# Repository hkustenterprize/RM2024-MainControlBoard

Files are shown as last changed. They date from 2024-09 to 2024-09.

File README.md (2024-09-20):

<div align='center'>
    <h1>灵活, 小巧, 可靠</h1>
</div>

<div align='center'>
    <h2>RM2024香港科技大学ENTERPRIZE</h2>
</div>

<div align='center'>
    <h1>G4主控板硬件开源</h1>
</div>

<div align='center'>

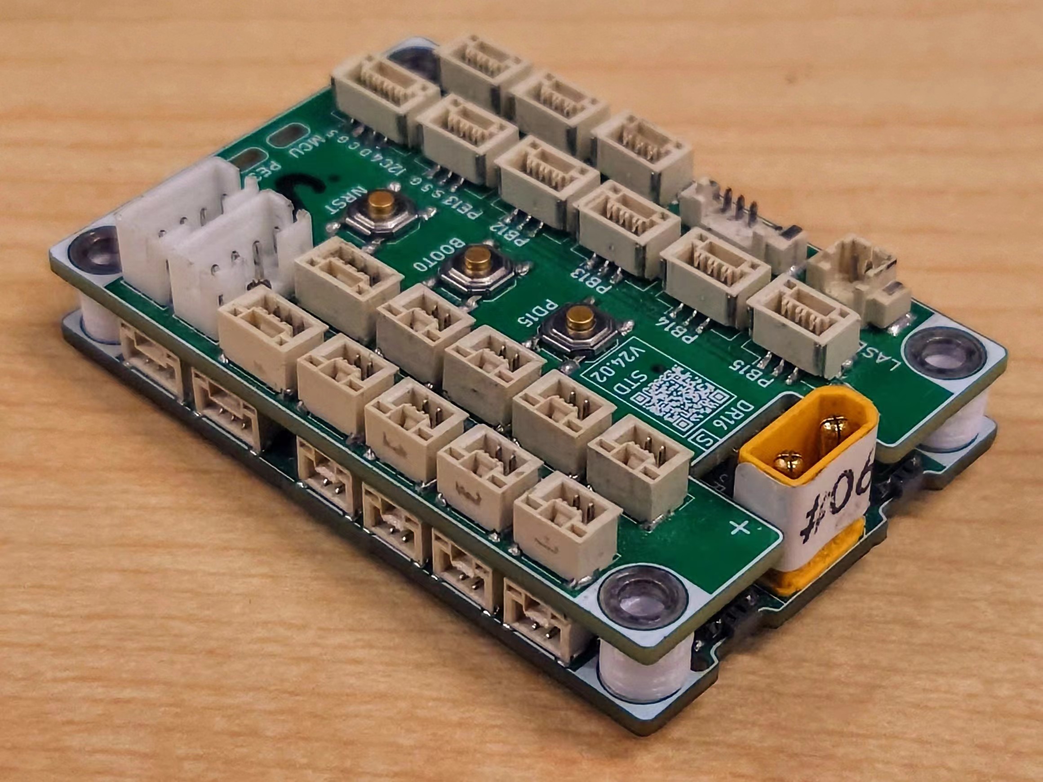
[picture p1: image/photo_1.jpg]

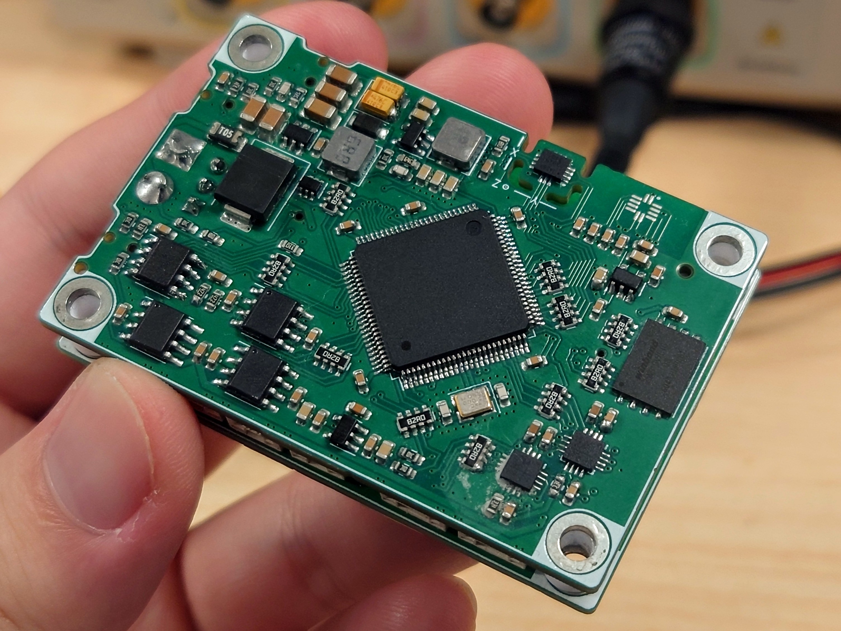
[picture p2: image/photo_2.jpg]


</div>

> 设计者：xzm/贤梓铭 zxianaa@connect.ust.hk
>
> 指导/提议：jyc/EthenJ, jason chan, ry/EEASEE, ofr, gzl/Fallengold, zzy
>
> 香港科技大学ENTERPRIZE战队 robomasterhkust@gmail.com

## 开源内容

~~~
RM2024_MainControlBoard
├── image
├── PDF Schematic               > PDF格式的原理图
├── RM2024_G473_MCB             > 核心板工程文件
├── RM2024_G473_MCB_Debugger    > 调试小板工程文件
├── RM2024_G473_MCB_EngExtend   > 单板方案工程扩展板工程文件 by ofr
├── RM2024_G473_MCB_StdExtend   > 常规扩展板工程文件
├── RM2024_G473_MCB_Shim.step   > 一体3D打印垫片step文件 by tsl
├── RM2024-Template-G473.ioc    > CubeMX模板
├── LICENSE
└── README.md
~~~

开源工程文件设计软件为 KiCAD, 建议使用 **KiCAD 8.0** 打开, 可以导入 **立创EDA**

每个工程文件文件夹中的内容:

~~~
xxx
├── bom             > 焊接小工具, 由 "Interactive HTML BOM" 插件生成
├── production      > 生产文件, 由 "Fabrication Toolkit" 插件生成
├── xxx.kicad_pcb   > PCB
├── xxx.kicad_pro   > 主工程, 通过双击这个启动KiCAD
└── xxx.kicad_sch   > 原理图
~~~

## 方案简介

整套主控板分为核心板(下板)和扩展板(上板), 两板之间使用80pin BTB接口连接; 核心板包含所有核心芯片, 而扩展板一般只用于引出接口 (以及buzzer, laser等功能), 需要特殊功能时则用作功能扩展

- MCU: STM32G473VET6
- IMU: ICM-42688P
- 磁力计: LIS3MDLTR
- TTL (硬件流控): CH343P *2 
- FDCAN *3
- RS485 (硬件流控) *1
- FLASH: W25N01GVZEIG

## 项目背景 & 应用情况

在 RoboMaster 2024 赛季, 由于队内自研的上一代主控板 (F407) 已经无法满足对机器人控制的需求, 于是产生了设计新型主控板的需求

在经过反复考虑和对比后, 我们选择了STM32G473VET6作为主控芯片, 主要原因如下

- 共有三路FDCAN外设, 可以控制更多电机
- 支持RS485硬件流控功能, 提升板间通讯的稳定性
- 相较于H7系列复杂度较低, 开发难度与F4系列近似

同时, 新一代主控板也有缩小体积的需求, 整个主控板大小控制在 **60×40×21mm**, 与大疆C板相近, 便于机械安装

<div align='center'>
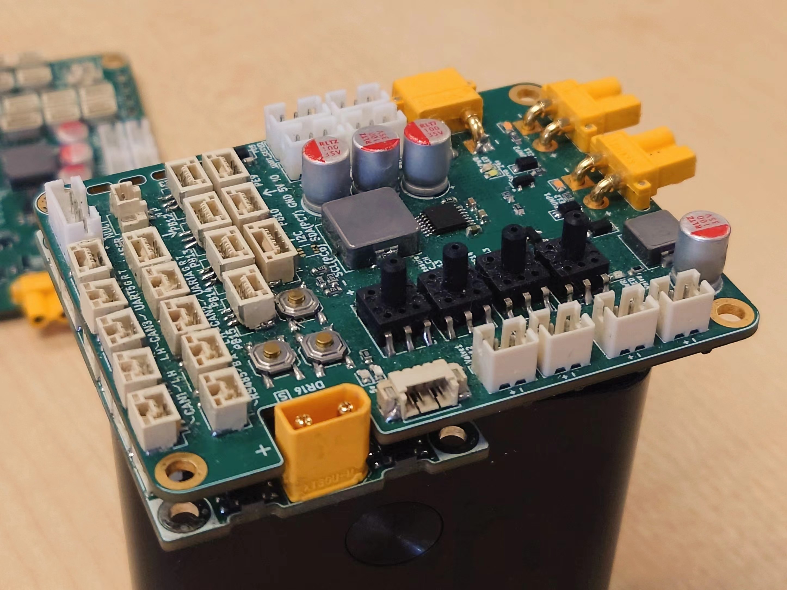
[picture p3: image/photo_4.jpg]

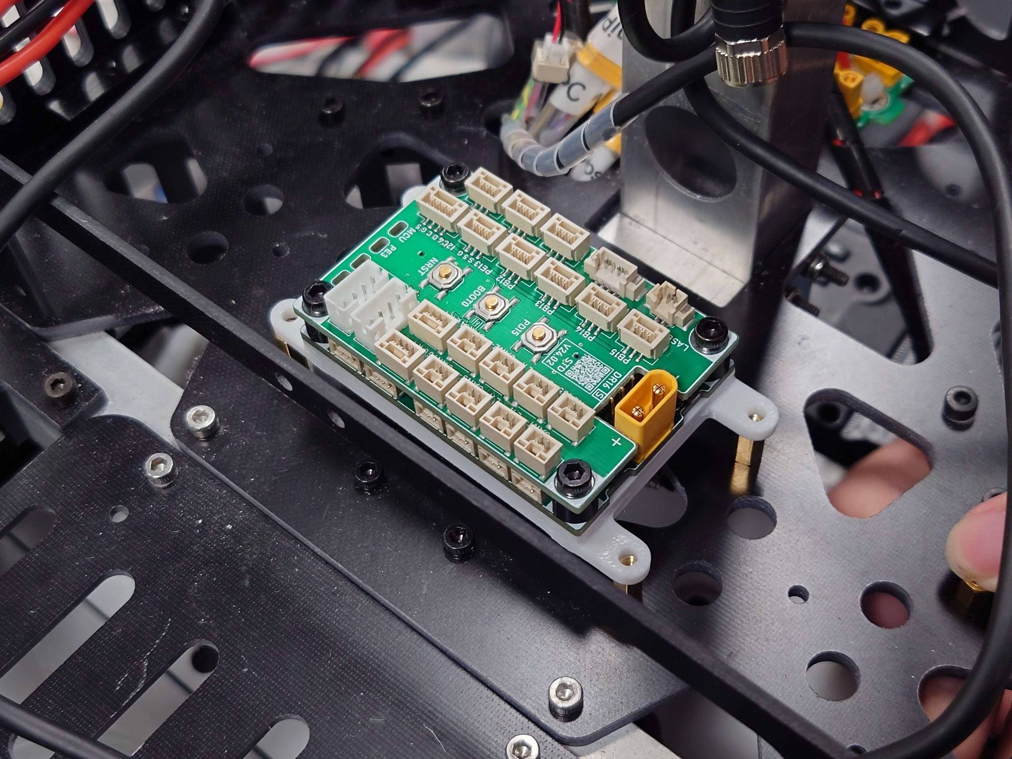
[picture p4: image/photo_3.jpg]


</div>

最终, G4主控板被应用于ENTERPRIZE战队本赛季所有新研发的机器人, 并且为 **工程机器人的单板方案** (左图) 和 **双头哨兵** (右图) 打下基础; 同时也实现了较强的稳定性, 在几场比赛中从未出现因硬件不稳定而导致的问题

## 硬件连接框图(简化)

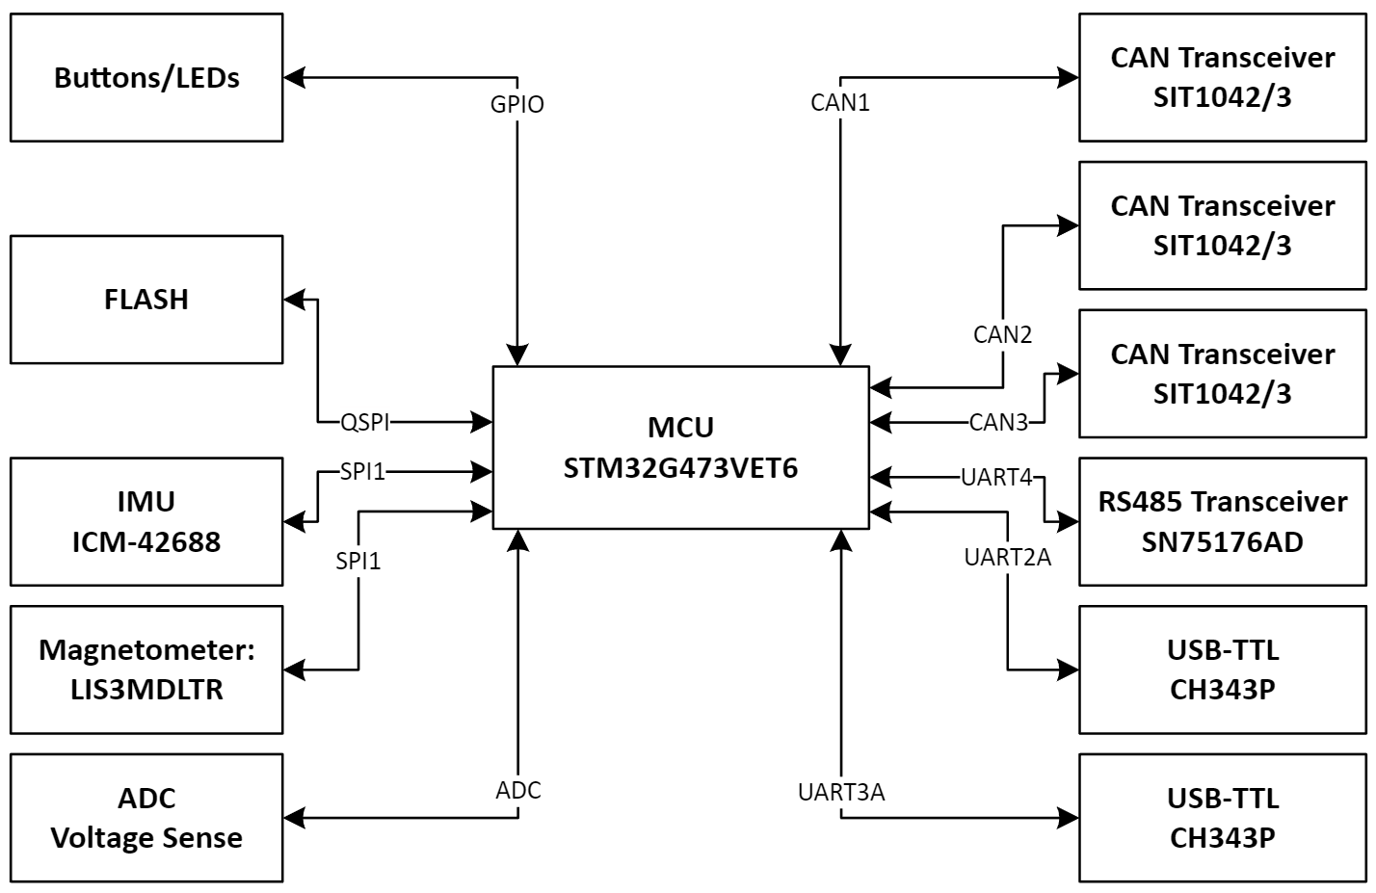
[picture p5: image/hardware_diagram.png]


## 技术细节

### UART

虽然STM32G473的FDCAN等外设数量较多, 但UART的数量却只有5个, 如果用传统的方法对UART和相应功能进行一一绑定, 那么UART数量则不足以实现所有需要的功能

为了解决此问题, G4主控板在设计时利用了MCU外设内部的 **MUX**, 比如 UART1 可以配置为 PC4/PC5 或 PE0/PE1, 再与相应功能进行绑定, 以此来实现在不同应用场景中适应不同需求的能力

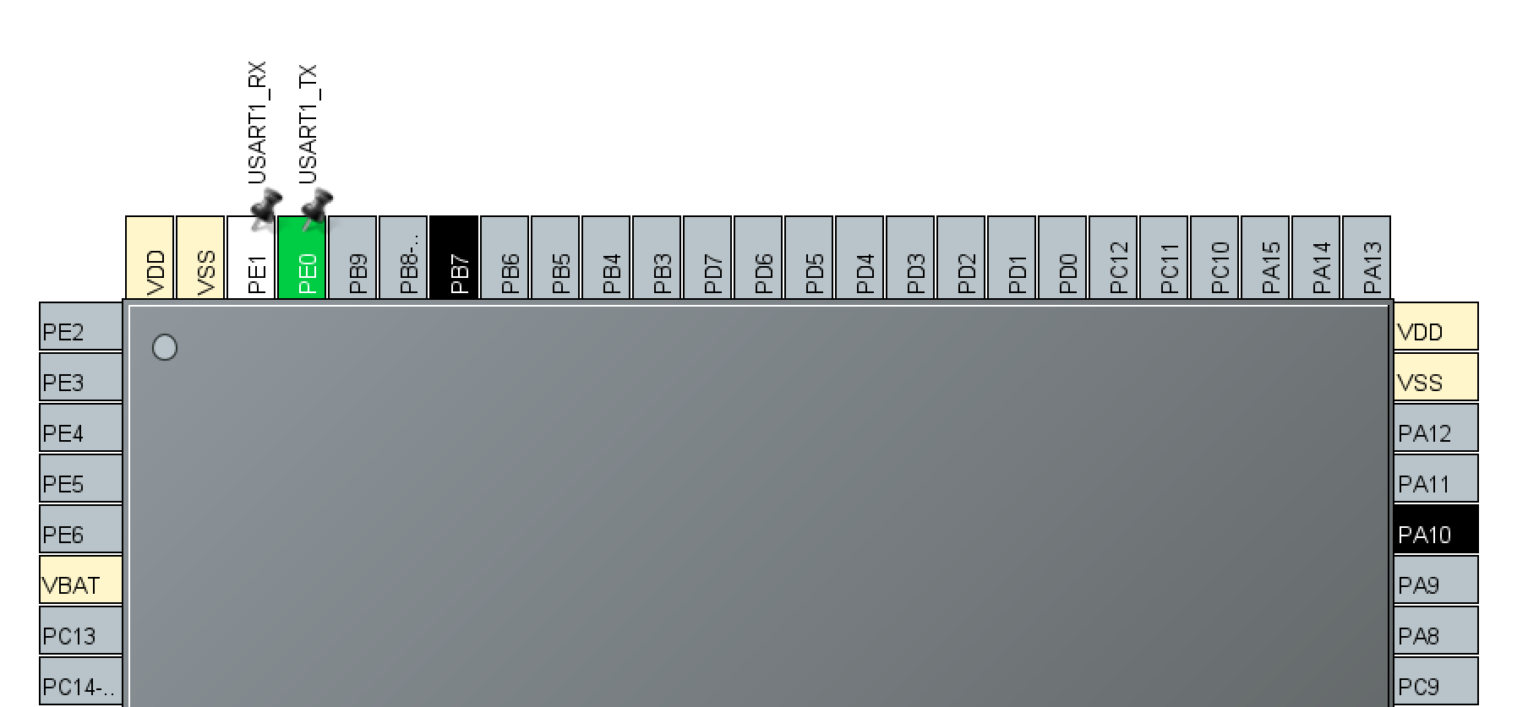
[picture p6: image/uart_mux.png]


同时, 对于同一功能, G4主控板也提供了可以从多个外设的访问的选项; 比如对于接收机, 可以通过软件配置来使用 UART1 或 UART3 来接受数据

下面是具体的UART引脚配置, 以A/B/C后缀来表示同一UART的不同配置方式:

| | TX | RX | DE | CTS  | RTS  | 功能 |
| -----  | ---- | ---- | ---- | ---- | ---- | ---- |
| UART1A | PC4  | PC5  | - | - | - | 裁判系统/图传  |
| UART1B | PE0  | PE1  | - | - | - | 通用 |
| UART1C | - | PA10 | - | - | - | 接收机 |
| UART2A | PA2  | PA3  | - | PA0  | PA1  | TTL1 |
| UART2B | PD5  | PD6  | - | - | - | 通用 |  
| UART3A | PD8  | PD9  | - | PD11 | PD12 | TTL2 |
| UART3B | PB10 | PE15 | - | - | - | 通用 |  
| UART3C | - | PB11 | - | - | - | 接收机 | 
| UART4  | PC10 | PC11 | PA15 | - | - | RS485 | 
| UART5  | PC12 | PD2  | - | - | - | 裁判系统/图传 |

下面是部分机器人上的UART功能分配:

| | UART1 | UART2 | UART3 | UART4 | UART5 |
| ----- | ----  | ----  | ----  | ----  | ----  |
| 步兵云台 | [C] 接收机 | [A] TTL1 | RESV | RS485 | [A] 图传 |
| 英雄云台 | [C] 接收机 | [A] TTL1 | RESV | RS485 | [A] 图传 |
| 哨兵云台 | [C] 接收机 | [A] TTL1 | [A] TTL2 | RS485 | [A] 图传 |
| 工程(单板) | [A] 裁判系统 | [B] 总线舵机  |  [C] 接收机 | RS485 | [A] 图传|
| 通用底盘  | RESV | RESV | RESV | RS485 | 裁判系统 |

### IMU

经过对比测试, IMU选择ICM-42688P, 并配合加热电阻实现恒温

经过测试, 选用1206封装, 36ohm的电阻可以满足恒温50°C的需求; 经测试, **恒温后纯IMU姿态解算5分钟内漂移小于1°**

同时, SPI信号线串接82ohm电阻, **通信速率可以稳定20M**

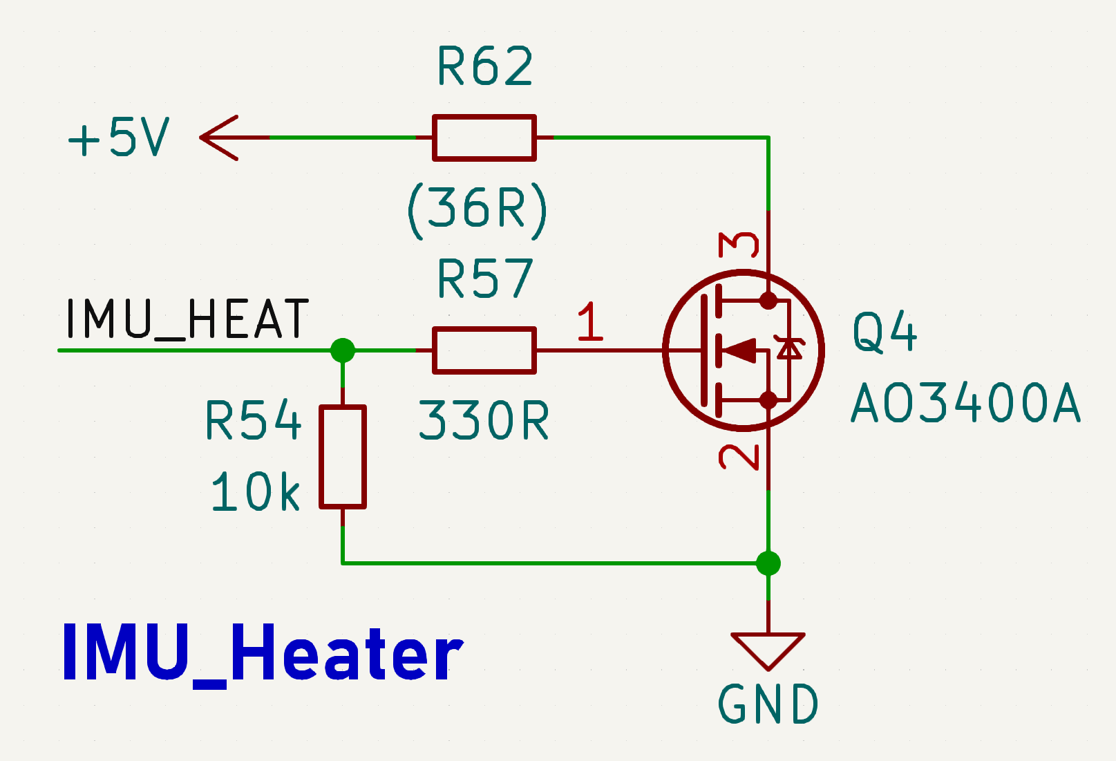
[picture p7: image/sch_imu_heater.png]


### RS485

| | TX/D | RX/R | DE |
| ----- | ---- | ---- | ---- |
| RS485 | PC10 | PC11 | PA15 |

主控板集成RS485来提供板间通信功能, 相较于串口, RS485可以使通信更加稳定(特别是过滑环时)

RS485 Transceiver选用SN75176AD, 可替换为其他芯片; 用SM712进行保护

使用STM32G473的RS485硬件流控功能后, **板间通信速率最高可以达到4.8M, 丢包率小于0.09%**

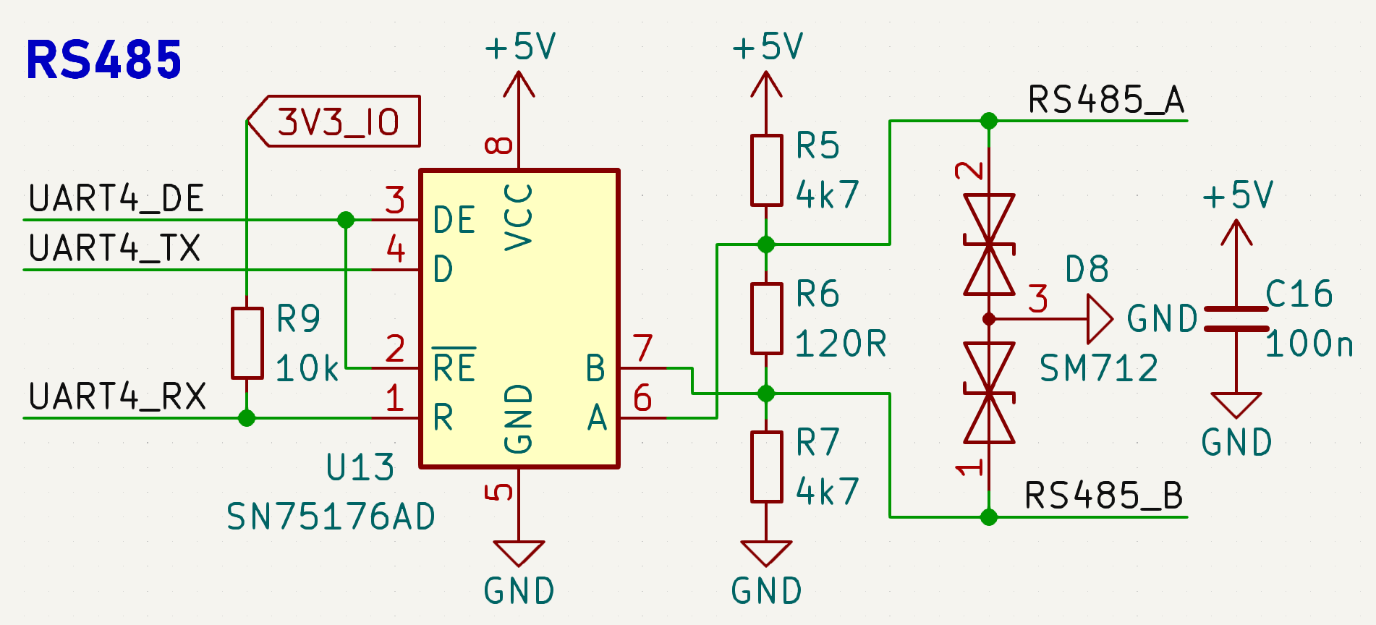
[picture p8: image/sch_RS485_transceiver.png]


### CAN (×3)

| | TX | RX |
| ----- | ---- | ---- |
| CAN1  | PD1  | PD0  |
| CAN2  | PB6  | PB5  |
| CAN3  | PB4  | PB3  |

CAN Transceiver选用SIT1042T/3, 可替换为其他芯片; 使用ESD1CAN进行保护

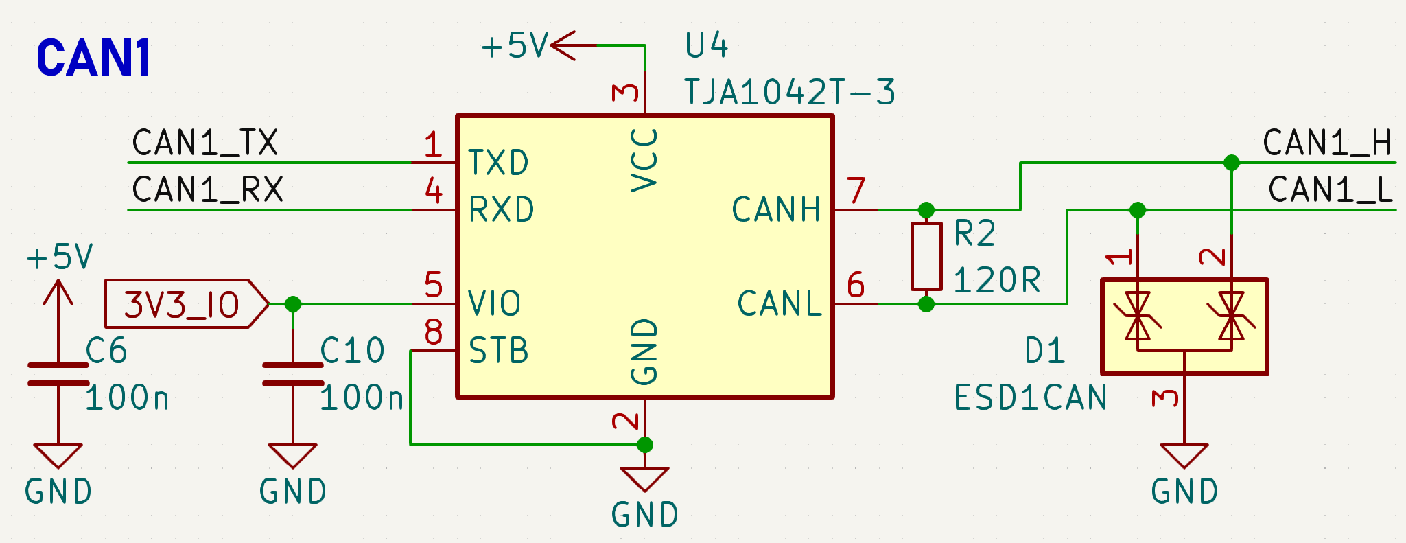
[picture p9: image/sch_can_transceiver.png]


### USB-TTL (×2)

| | TX | RX | CTS  | RTS  |
| ----- | ---- | ---- | ---- | ---- |
| TTL1 (UART2A)  | PA2  | PA3  | PA0  | PA1  |
| TTL2 (UART3A)  | PD8  | PD9  | PD11 | PD12 |

USB-TTL选用CH343P, 连接了RTS/CTS引脚来实现硬件流控, 使用TPD4E1U06DCKR进行保护

经测试**全双工条件下单向速率稳定2M, 实测丢包率0.006%左右**

连接了ACT指示灯, 方便观察连接状态, 此功能上场时非常有用(观察MiniPC是否断连)

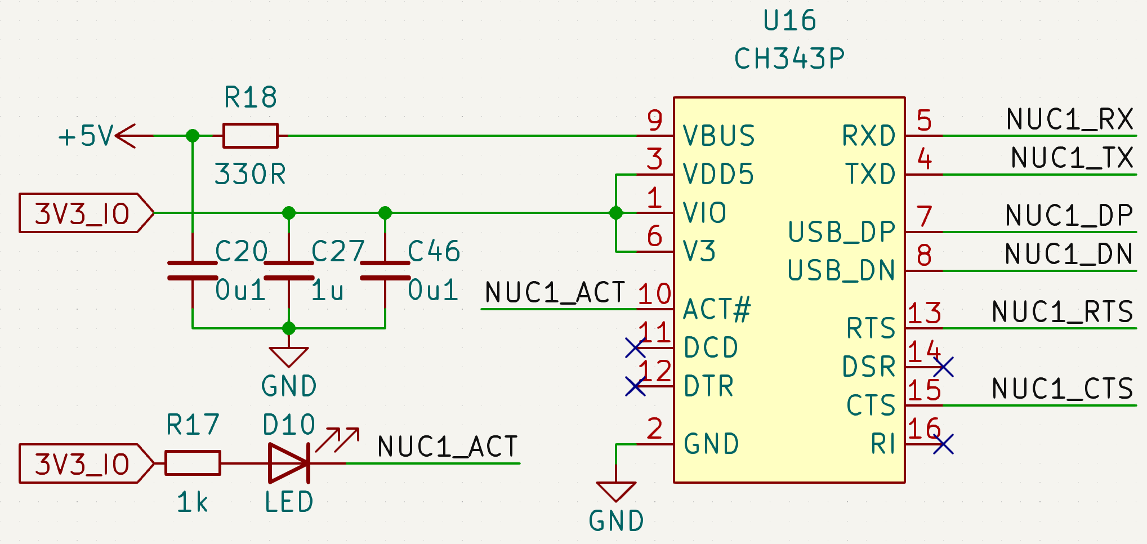
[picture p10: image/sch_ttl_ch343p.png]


### FLASH

| | NCS | CLK | IO0  | IO1  | IO2  | IO3  |
| ----- | ---- | ---- | ---- | ---- | ---- | ---- |
| MCU | PD3  | PF10  | PD4  | PC2  | PD3  | PC7  |

主控板集成FLASH用于记录数据, 便于调试分析; 型号选用W25N01GVZEIG; 通过QSPI与MCU进行通信

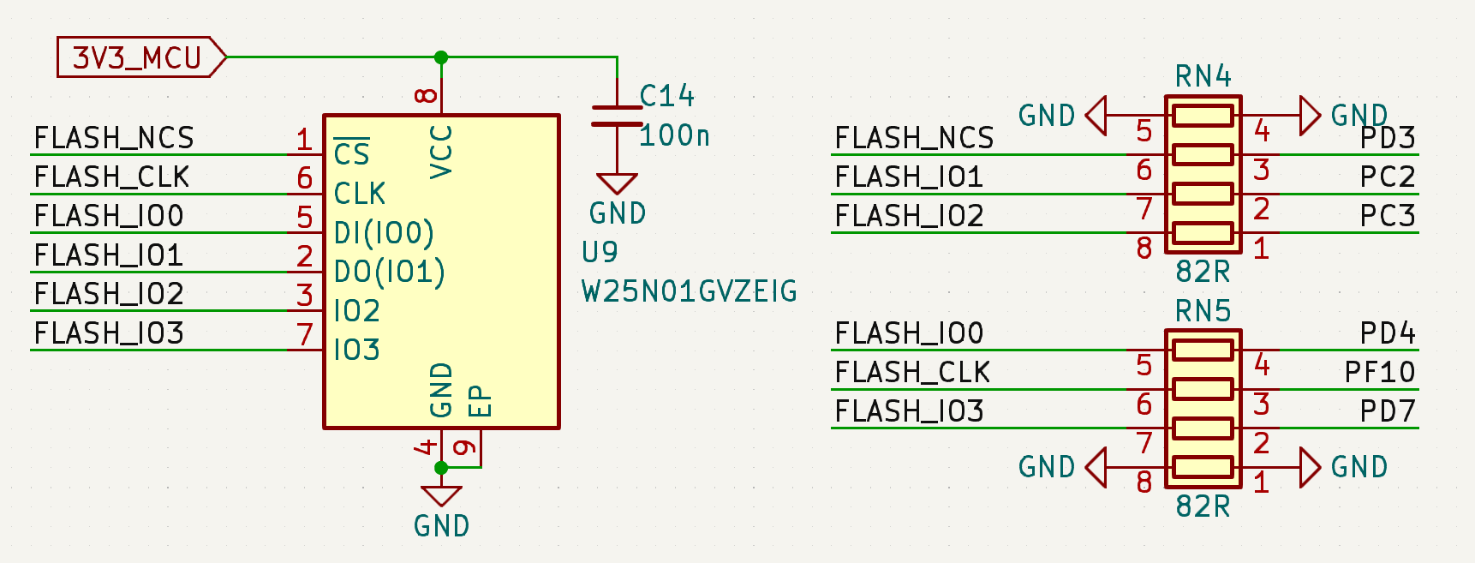
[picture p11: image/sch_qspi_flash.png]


### 接收机

G4主控板采用MCU内部反相, 无需外部反相电路, 使用TPD4E1U06DCKR进行保护

可以通过 PB11(UART3) 或 PA10(UART1) 接收信号, 防止其中一个串口被占用的情况

### 硬件ID检测

通过短接扩展板上的三个ID焊盘, 可以配置主控板的 ID 和 Master/Slave角色

通过在代码中加入ID验证步骤, 可以防止因烧错代码导致 RS485 Transceiver 烧毁等问题

## 供电系统

### 电源框图

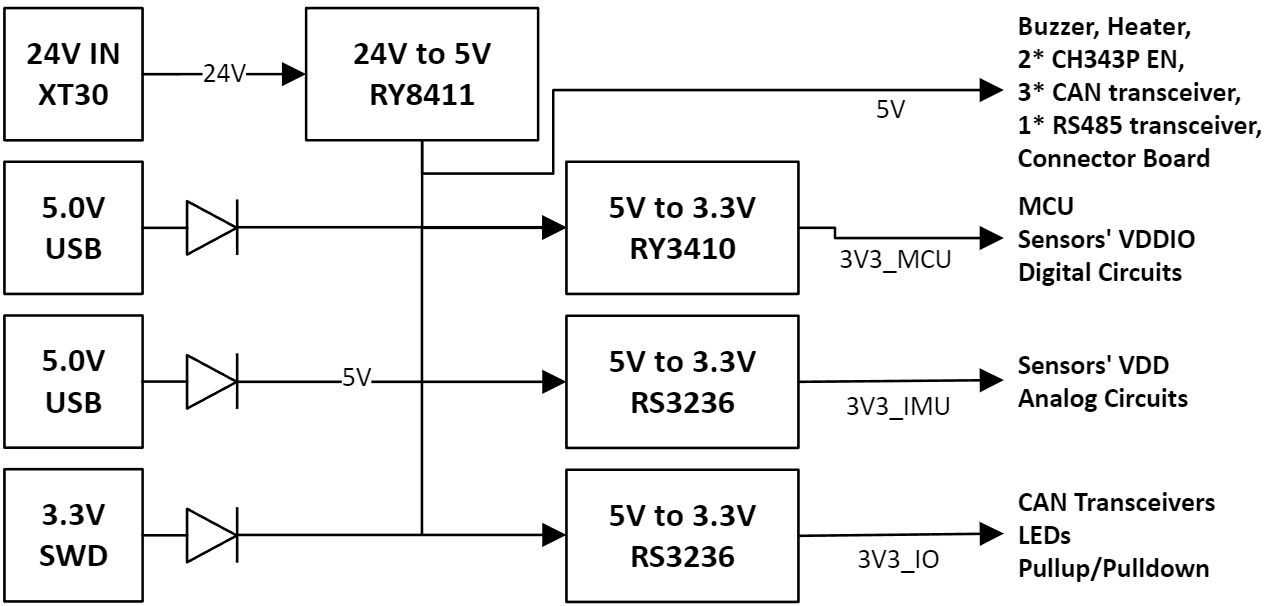
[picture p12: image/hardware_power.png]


### 设计细节及原因

#### 3V3_MCU

由Buck电路而非LDO降压产生, 原因是STM32G473耗电量较大, 使用LDO会有潜在的过热问题; 

同时, 主控板上没有高精度ADC的需求, 故Buck电路的纹波对主控板正常工作影响不大

#### 3V3_IMU

专门用于IMU和磁力计的 VDD 供电网络, 防止其他噪声干扰IMU和磁力计; 

注意IMU和磁力计的 VDDIO 由 3V3_MCU 提供, 防止芯片内部通信部分对电源产生潜在干扰

#### 3V3_IO

主要用于于外部直接产生交互的外设的VIO;

与 3V3_MCU 隔离, 主要原因是为了防止外部收发信号时对核心供电的干扰, 比如 CAN 和 TTL 都直接使用 3V3_IO 作为生成信号电平的电源

#### 3V3_SWD

队内发生过因烧录器LDO损坏而导致 5V 烧毁MCU, 因此与 3V3_MCU 隔离, 通过二极管接入5V网络并同时防止倒灌;

此设计也产生了一个缺陷: 当主控板仅由烧录器供电是, 有时会因为压降太大而导致烧录不正常, 因此建议在有MiniPC USB供电或24V供电的情况下进行代码烧录和调试

#### 电压采样

主控板对 24V 和 5V 电源网络进行了电压采样;

前者是为了监测 24V 真实电源电压, 可以得到一些粗略电压信息;

后者是通过检测微小电压差异来确定目前的供电方式 (利用Buck输出 5.2V, USB供电 5.0V, SWD供电三种情况导致的差异), 并且在状态不正常时报警 (比如可以检测24V转5V的Buck损坏)

### 纹波测试
5V

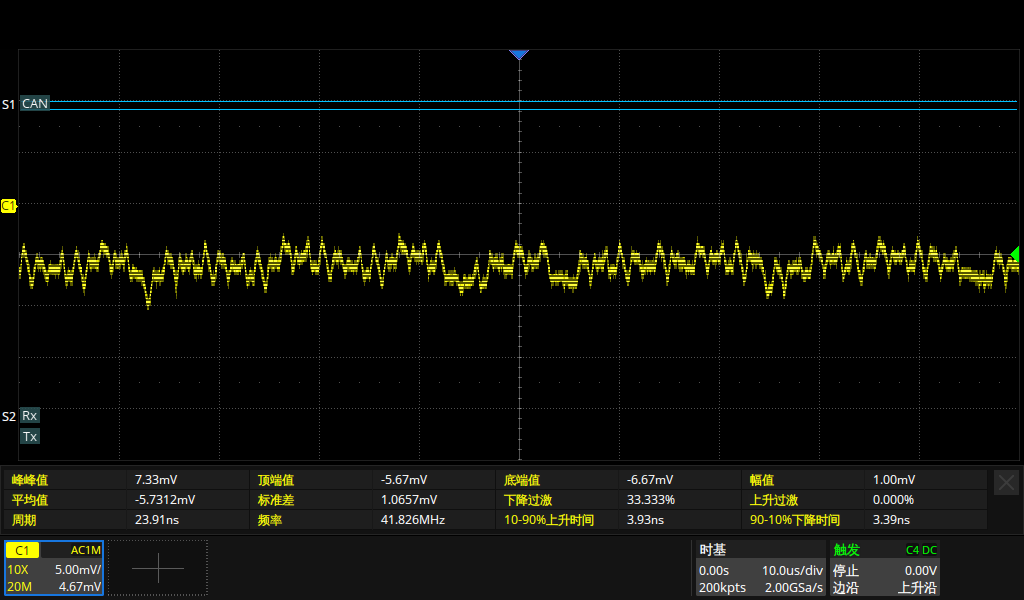
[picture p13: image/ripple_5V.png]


3V3_MCU

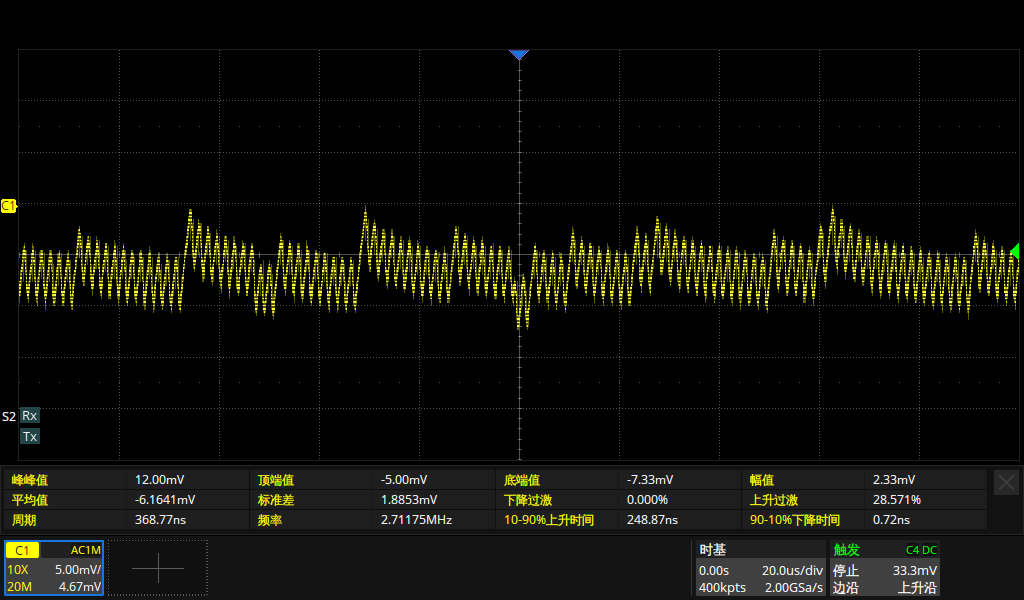
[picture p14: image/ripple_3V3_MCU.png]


## 复刻注意事项

- 目前包含的SMT生产文件格式适用于嘉立创, 如有需要请重新生成
- BTB很脆弱, 避免在不垫垫片的情况下安装
- 焊接IMU后不要用超声波洗板
- 如有任何问题, 欢迎联系 zxianaa@connect.ust.hk; wx: xianziming0531

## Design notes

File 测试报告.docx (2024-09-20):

HKUST RoboMaster Team ENTERPRIZE

RM2024 G4主控板测试报告

电源波形 - 5V网络


电源波形 - 3V3_MCU网络


RS485

板间通信速率最高可以达到4.8M, 丢包率小于0.09%

USB-TTL

全双工条件下单向速率稳定2M, 实测丢包率0.006%左右

焊接和测试流程

1. 焊接电源部分RY8411, RY3410, LDO, 保险丝, TVS

2. 测试5V, 3V3_MCU, 3V3_IO, 3V3_IMU电源电压和纹波

3. 焊接CH343P, SIT1042T/3, SN65HVD1176

4. 焊接Solder the rest of the board except the BTB connector and IMU (ICM-42688) and Magnetometer (LIS3MDLTR)

6. Wash the board. Check if the MCU is alive, then test CAN*3 and RS485 (ask software).

7. Solder the BTB connector and IMU (ICM-42688) and Magnetometer (LIS3MDLTR)

*Do not use ultrasonic washer after soldering IMU and Magnetometer

8. Solder the Connector Board

*Cut short the pins of the PH2.0 4pin connectors to prevent intervene.

9. Full function test (ask software).

10. 3D print a shell (ask mech).

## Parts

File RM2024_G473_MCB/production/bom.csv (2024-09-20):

Designator | Footprint | Quantity | Value | LCSC Part #
C1, C10, C11, C12, C14, C16, C2, C21, C3, C37, C4, C40, C42, C45, C48, C5, C52, C54, C55, C56, C57, C58, C59, C6, C7, C70, C71, C8, C9 | 0603 | 29 | 100n
C13, C23, C28 | CP_EIA-3216-18_Kemet-A_Pad1.58x1.35mm_HandSolder | 3 | 47u
C17, C20, C46, C47 | 0603 | 4 | 0u1
C19, C27 | 0603 | 2 | 1u
C22, C50, C60, C61 | 0603 | 4 | 20p
C24, C25, C26, C29, C30 | 1206 | 5 | 10u
C36, C39, C41, C44, C51, C53, C63, C64, C65, C76, C78 | 0603 | 11 | 10u
C38, C43 | 0603 | 2 | 10n
D1, D2, D3 | SOT-23 | 3 | NUP2105L
D10, D11 | 0603 | 2 | LED
D12 | D_SMF | 1 | 3V3 TVS
D14, D6 | D_SMF | 2 | K34
D22 | 0603 | 1 | 3V3
D23 | 0603 | 1 | ACT
D4 | D_SMC | 1 | SMCJ28A
D5 | D_SMA | 1 | SMAJ5.0A
D8 | SOT-23 | 1 | SM712
F1 | 1206 | 1 | Fuse
H1, H2, H3, H4 | MountingHole_3.2mm_M3_DIN965_Pad | 4 | M3.2 Mount
J1 | BTB_P0.8mm_2x40pin_F | 1 | BTB
J2 | JST_GH_SM02B-GHS-TB_1x02-1MP_P1.25mm_Horizontal | 1 | RS-485
J20 | AMASS_XT30U-M_1x02_P5.0mm_Vertical | 1 | PWRIn
J22 | PinHeader_1x03_P2.54mm_Vertical | 1 | D-Bus
J28 | Molex_PicoBlade_53261-0471_1x04-1MP_P1.25mm_Horizontal | 1 | SWD
J3 | JST_GH_SM02B-GHS-TB_1x02-1MP_P1.25mm_Horizontal | 1 | CAN1
J4 | JST_GH_SM02B-GHS-TB_1x02-1MP_P1.25mm_Horizontal | 1 | CAN2
J5 | JST_GH_SM02B-GHS-TB_1x02-1MP_P1.25mm_Horizontal | 1 | CAN3
J6 | JST_GH_SM03B-GHS-TB_1x03-1MP_P1.25mm_Horizontal | 1 | UART1A
J7 | JST_GH_SM03B-GHS-TB_1x03-1MP_P1.25mm_Horizontal | 1 | UART5
L1 | L_Sunlord_MWSA0402S | 1 | 6u8
L2 | 0603 | 1 | 220r
L3 | L_Sunlord_MWSA0402S | 1 | 4u7
Q4 | SOT-23 | 1 | AO3400A
R1, R10, R12, R15, R16, R17, R51, R52 | 0603 | 8 | 1k
R11, R21, R22, R24, R25, R26, R32, R54, R59, R61, R9 | 0603 | 11 | 10k
R18, R19, R31, R57, R58, R60 | 0603 | 6 | 330R
R2, R3, R4, R6 | 0603 | 4 | 120R
R20 | 0603 | 1 | 47k
R23 | 0603 | 1 | 54k6
R5, R7 | 0603 | 2 | 4k7
R62 | 1206 | 1 | (36R)
R8 | 0603 | 1 | 33R
RN1, RN12, RN13, RN19, RN2, RN20, RN21, RN3, RN4, RN5 | R_Array_Concave_4x0603 | 10 | 82R
SW1 | Panasonic_EVQPUL_EVQPUC | 1 | NRST
SW2 | Panasonic_EVQPUL_EVQPUC | 1 | BOOT0
SW4 | Panasonic_EVQPUL_EVQPUC | 1 | BTN
U1 | LQFP-100_14x14mm_P0.5mm | 1 | STM32G473VETx
U10, U11 | SOT-23-5 | 2 | RS3236
U12, U4, U7 | SOIC-8_3.9x4.9mm_P1.27mm | 3 | TJA1042T-3
U13 | SOIC-8_3.9x4.9mm_P1.27mm | 1 | SN75176AD
U14 | SOT-23-5 | 1 | RY3430
U16, U17 | TQFN-16-1EP_3x3mm_P0.5mm_EP1.6x1.6mm | 2 | CH343P
U2 | PQFN50P300X250X97-14N | 1 | ICM-42688-P
U3 | XDCR_LIS3MDLTR | 1 | LIS3MDLTR
U5, U6 | SOT-363_SC-70-6 | 2 | TPD4E1U06DCKR
U8 | SOT-23-6 | 1 | RY8411
U9 | WSON-8-1EP_8x6mm_P1.27mm_EP3.4x4.3mm | 1 | W25Q32JVZP
Y1 | Crystal_SMD_3225-4Pin_3.2x2.5mm | 1 | 3225 25MHz

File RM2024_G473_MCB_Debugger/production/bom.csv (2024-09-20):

Designator | Footprint | Quantity | Value | LCSC Part #
BZ1 | MLT-9032 | 1 | Buzzer
C1 | 0603 | 1 | 100n
C2, C3 | 0603 | 2 | 10u
D1 | D_SMF | 1 | K34
D2 | 0603 | 1 | G
J2 | Molex_PicoBlade_53398-0471_1x04-1MP_P1.25mm_Vertical | 1 | SWD
J3 | JST_GH_SM07B-GHS-TB_1x07-1MP_P1.25mm_Horizontal | 1 | Conn_01x07_MountingPin
R1, R2 | 0603 | 2 | 10k
U1 | SSOP-28_3.9x9.9mm_P0.635mm | 1 | TM1640(TA2103) SSOP-28
U2 | LED-8888-3461 | 1 | 3461

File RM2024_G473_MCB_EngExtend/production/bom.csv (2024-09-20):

Designator | Footprint | Quantity | Value | LCSC Part #
BZ1 | MLT-9032 | 1 | Buzzer
C1, C13, C25, C26, C27, C28, C29, C30, C31, C32, C33, C5, C6, C7, C8 | 0603 | 15 | 100n
C10, C11, C12, C2, C39, C9 | 0603 | 6 | 10u
C14, C17, C35, C38 | CP_Radial_D6.3mm_P2.50mm | 4 | C_Polarized
C15 | 0603 | 1 | 10n
C16 | 0603 | 1 | 15n
C18 | 0603 | 1 | 2.2u
C19 | 1206 | 1 | C
C20 | 0603 | 1 | 470n
C21, C22 | 0603 | 2 | 100p
C23, C24, C3, C36, C37, C4 | 1206 | 6 | 10u
C34 | 0603 | 1 | 47p
C40 | 0603 | 1 | 20p
D1, D10, D6, D9 | D_SMF | 4 | SMF10A
D11, D13, D14, D17, D2, D8 | D_SMF | 6 | DSS34
D12, D15, D16, D18, D19, D20, D24, D25, D26, D27, D28, D29 | 0603 | 12 | LED
D21, D3, D5 | D_SMF | 3 | K34
D22 | D_SMA | 1 | DSS34
D23 | D_SMC | 1 | SMC
D4 | D_SMF | 1 | SMF3V3A
D7 | D_SMF | 1 | D_Schottky
F1 | 1206 | 1 | 8A 1206
H1, H2, H3, H4, H5, H6 | MountingHole_3.2mm_M3_DIN965_Pad | 6 | MountingHole
J1 | JST_PH_B4B-PH-K_1x04_P2.00mm_Vertical | 1 | USB
J10 | JST_GH_BM02B-GHS-TBT_1x02-1MP_P1.25mm_Vertical | 1 | CAN3
J11, J12, J13 | JST_GH_BM02B-GHS-TBT_1x02-1MP_P1.25mm_Vertical | 3 | CAN2
J14 | Molex_PicoBlade_53261-0471_1x04-1MP_P1.25mm_Horizontal | 1 | SWD
J15 | BTB_P0.8mm_2x40pin_M | 1 | BTB
J16, J18, J19, J20, J23, J24 | JST_GH_BM03B-GHS-TBT_1x03-1MP_P1.25mm_Vertical | 6 | Conn_01x03_MountingPin
J17, J28, J29, J34 | JST_PH_B2B-PH-K_1x02_P2.00mm_Vertical | 4 | Conn_01x02
J2, J27 | AMASS_XT30PW-F_1x02_P2.50mm_Horizontal | 2 | Relay_1
J21, J31, J35 | JST_PH_B3B-PH-K_1x03_P2.00mm_Vertical | 3 | Conn_01x03
J25 | JST_GH_BM04B-GHS-TBT_1x04-1MP_P1.25mm_Vertical | 1 | Conn_01x04_MountingPin
J26 | AMASS_XT30PW-M_1x02_P2.50mm_Horizontal | 1 | PWR_IN
J3 | JST_GH_BM03B-GHS-TBT_1x03-1MP_P1.25mm_Vertical | 1 | UART1A
J4 | JST_GH_BM03B-GHS-TBT_1x03-1MP_P1.25mm_Vertical | 1 | UART5
J5, J9 | JST_GH_BM02B-GHS-TBT_1x02-1MP_P1.25mm_Vertical | 2 | RS-485
J6, J7 | JST_GH_BM02B-GHS-TBT_1x02-1MP_P1.25mm_Vertical | 2 | CAN1
J8 | Molex_PicoBlade_53261-0271_1x02-1MP_P1.25mm_Horizontal | 1 | Laser
JP1 | SolderJumper-3_P1.3mm_Open_RoundedPad1.0x1.5mm_NumberLabels | 1 | ID0
JP2 | SolderJumper-3_P1.3mm_Open_RoundedPad1.0x1.5mm_NumberLabels | 1 | ID1
JP3 | SolderJumper-3_P1.3mm_Open_RoundedPad1.0x1.5mm_NumberLabels | 1 | ID3
L1 | L_Sunlord_MWSA0603S | 1 | L
L2 | L_Wuerth_HCI-1040 | 1 | 4.7u
Q1, Q12, Q4, Q7, Q8, Q9 | SOT-23 | 6 | AO3400A
Q10, Q2 | DFN-8-1EP_3x3mm_P0.65mm_EP1.5x2.25mm | 2 | NCE40P20Q
Q11, Q5 | TDSON-8-1_HandSolder | 2 | BSC070N10NS5
Q3, Q6 | SOT-23 | 2 | SI2300
R1, R10, R11, R12, R9 | 0603 | 5 | 4k7
R13, R14, R16, R18, R22, R23, R25, R3, R57, R58, R62, R63 | 0603 | 12 | 10k
R15, R24, R26, R29, R32, R35 | 0603 | 6 | 330
R17, R48, R49, R50, R52, R53, R54, R55 | 0603 | 8 | 4.7K
R19, R47 | 0603 | 2 | 1.13k
R2, R6, R7 | 0603 | 3 | 33R
R20, R56 | 0603 | 2 | 73.2k
R21, R27, R28, R30, R31, R33, R34, R36, R51, R61, R65 | 0603 | 11 | 100k
R37, R38, R39, R40, R41, R42, R43, R44 | 0603 | 8 | 200k
R4, R5, R59, R64, R8 | 0603 | 5 | 330R
R45, R46, R60 | 0603 | 3 | 240k
RN1, RN2 | R_Array_Concave_4x0603 | 2 | 33R
SW1 | SW_SPST_TL3342 | 1 | BOOT0
SW2 | SW_SPST_TL3342 | 1 | NRST
SW3 | SW_SPST_TL3342 | 1 | BTN
U1, U2, U3 | SOT-363_SC-70-6 | 3 | TPD4E1U06DCKR
U10, U6, U7, U8 | pressure_sensor | 4 | ~
U4 | TI_SO-PowerPAD-8_ThermalVias | 1 | TPS5450
U5 | HTSSOP-14-1EP_4.4x5mm_P0.65mm_EP3.4x5mm_Mask3x3.1mm | 1 | LM3150MH
U9 | TSSOP-14_4.4x5mm_P0.65mm | 1 | GS8554

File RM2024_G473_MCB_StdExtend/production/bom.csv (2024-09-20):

Designator | Footprint | Quantity | Value | LCSC Part #
C1, C5, C6, C7 | 0603 | 4 | 100n
C10, C11, C12, C13, C2, C3, C4, C9 | 0603 | 8 | 10u
C14 | 0603 | 1 | 20p
C8 | CP_EIA-3216-18_Kemet-A_Pad1.58x1.35mm_HandSolder | 1 | 47u
D1, D4, D5, D6 | D_SMF | 4 | K34
D2 | LED_RGB_5050-6 | 1 | LED_RGB
D3 | D_SMF | 1 | SMF5V0A
F1 | 1206 | 1 | Fuse
H1, H2, H3, H4 | MountingHole_3.2mm_M3_DIN965_Pad | 4 | MountingHole
J1, J2 | JST_PH_B4B-PH-K_1x04_P2.00mm_Vertical | 2 | USB
J10 | JST_GH_BM02B-GHS-TBT_1x02-1MP_P1.25mm_Vertical | 1 | CAN3
J11, J12, J13 | JST_GH_BM02B-GHS-TBT_1x02-1MP_P1.25mm_Vertical | 3 | CAN2
J14 | Molex_PicoBlade_53398-0471_1x04-1MP_P1.25mm_Vertical | 1 | SWD
J15 | BTB_P0.8mm_2x40pin_M | 1 | BTB
J16, J18, J19, J20, J23 | JST_GH_BM03B-GHS-TBT_1x03-1MP_P1.25mm_Vertical | 5 | Conn_01x03_MountingPin
J17 | JST_GH_BM07B-GHS-TBT_1x07-1MP_P1.25mm_Vertical | 1 | Conn_01x07_MountingPin
J21, J25 | JST_GH_BM04B-GHS-TBT_1x04-1MP_P1.25mm_Vertical | 2 | Conn_01x04_MountingPin
J3 | JST_GH_BM03B-GHS-TBT_1x03-1MP_P1.25mm_Vertical | 1 | UART1A
J4 | JST_GH_BM03B-GHS-TBT_1x03-1MP_P1.25mm_Vertical | 1 | UART5
J5, J9 | JST_GH_BM02B-GHS-TBT_1x02-1MP_P1.25mm_Vertical | 2 | RS-485
J6, J7 | JST_GH_BM02B-GHS-TBT_1x02-1MP_P1.25mm_Vertical | 2 | CAN1
J8 | Molex_PicoBlade_53398-0271_1x02-1MP_P1.25mm_Vertical | 1 | Laser
JP1 | SolderJumper-3_P1.3mm_Open_RoundedPad1.0x1.5mm_NumberLabels | 1 | ID0
JP2 | SolderJumper-3_P1.3mm_Open_RoundedPad1.0x1.5mm_NumberLabels | 1 | ID1
JP3 | SolderJumper-3_P1.3mm_Open_RoundedPad1.0x1.5mm_NumberLabels | 1 | ID3
Q1, Q2, Q3, Q4, Q5 | SOT-23 | 5 | AO3400A
R1, R10, R11, R12, R9 | 0603 | 5 | 4k7
R13, R3 | 0603 | 2 | 10k
R14, R4, R5, R8 | 0603 | 4 | 330R
R16, R18, R20 | 0603 | 3 | 330
R2, R6, R7 | 0603 | 3 | 33R
RN1, RN2 | R_Array_Concave_4x0603 | 2 | 33R
SW4 | SW_SPST_PTS810 | 1 | BOOT0
SW5 | SW_SPST_PTS810 | 1 | NRST
SW6 | SW_SPST_PTS810 | 1 | BTN
U1, U2, U3 | SOT-363_SC-70-6 | 3 | TPD4E1U06DCKR

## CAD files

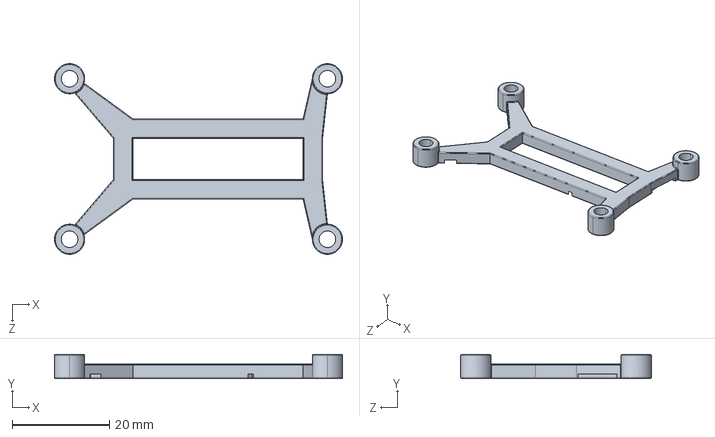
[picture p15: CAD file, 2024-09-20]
RM2024_G473_MCB_Shim.STEP
59.2 x 5.00 x 39.2 mm

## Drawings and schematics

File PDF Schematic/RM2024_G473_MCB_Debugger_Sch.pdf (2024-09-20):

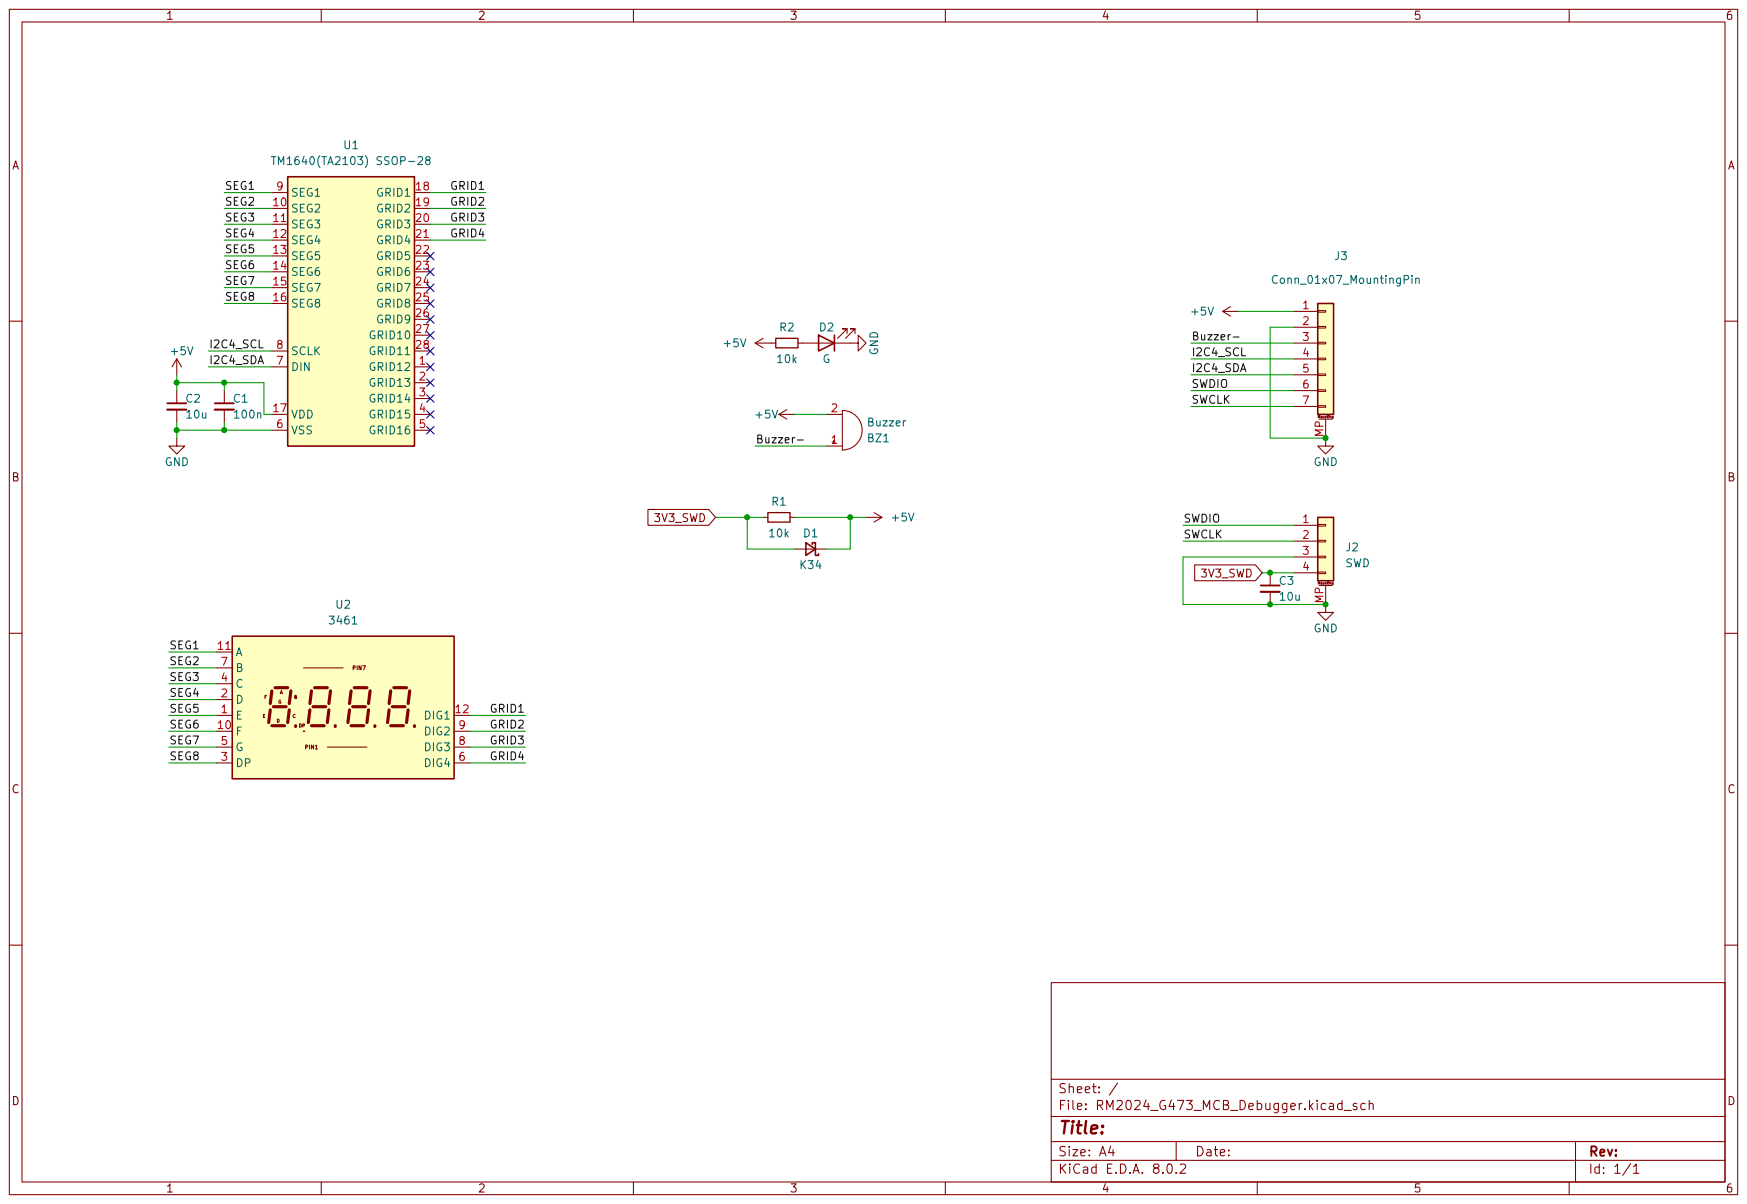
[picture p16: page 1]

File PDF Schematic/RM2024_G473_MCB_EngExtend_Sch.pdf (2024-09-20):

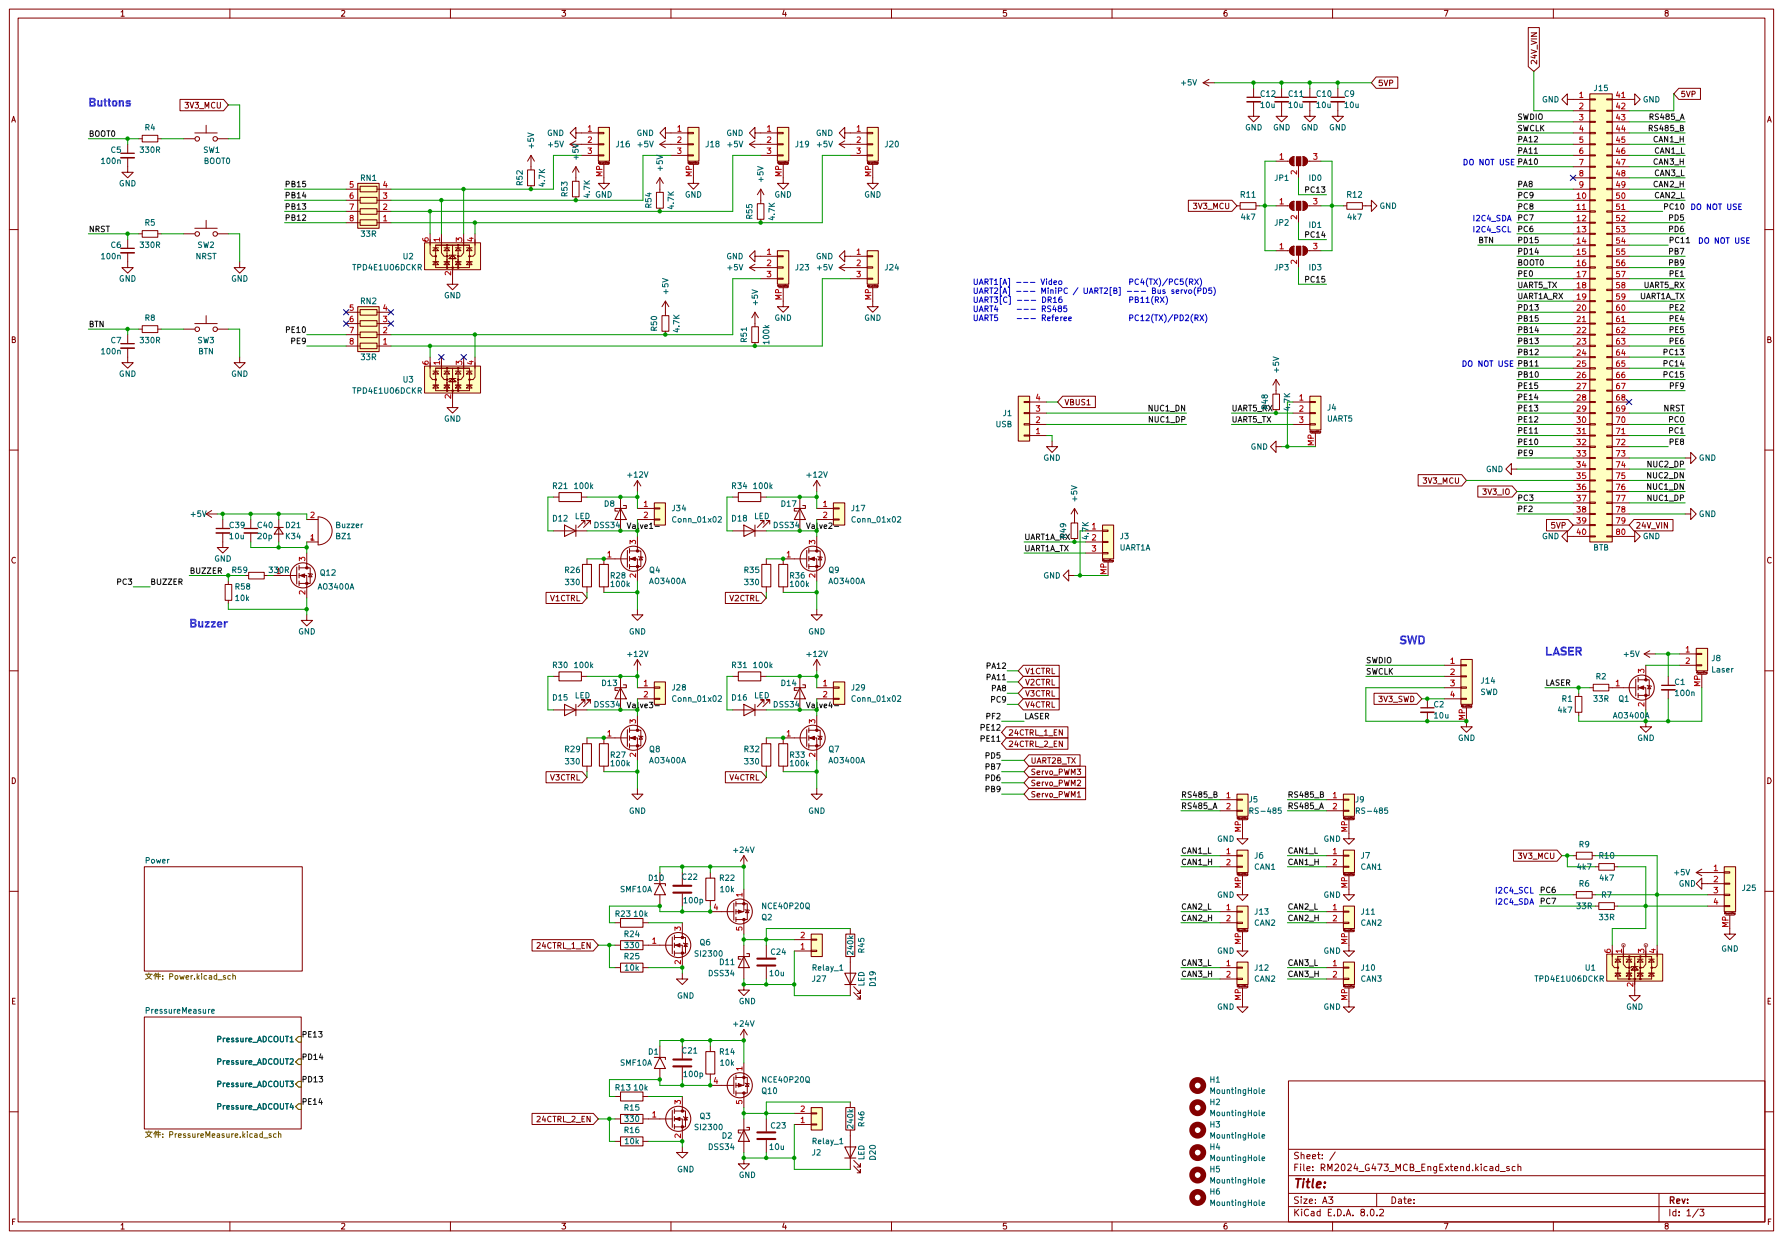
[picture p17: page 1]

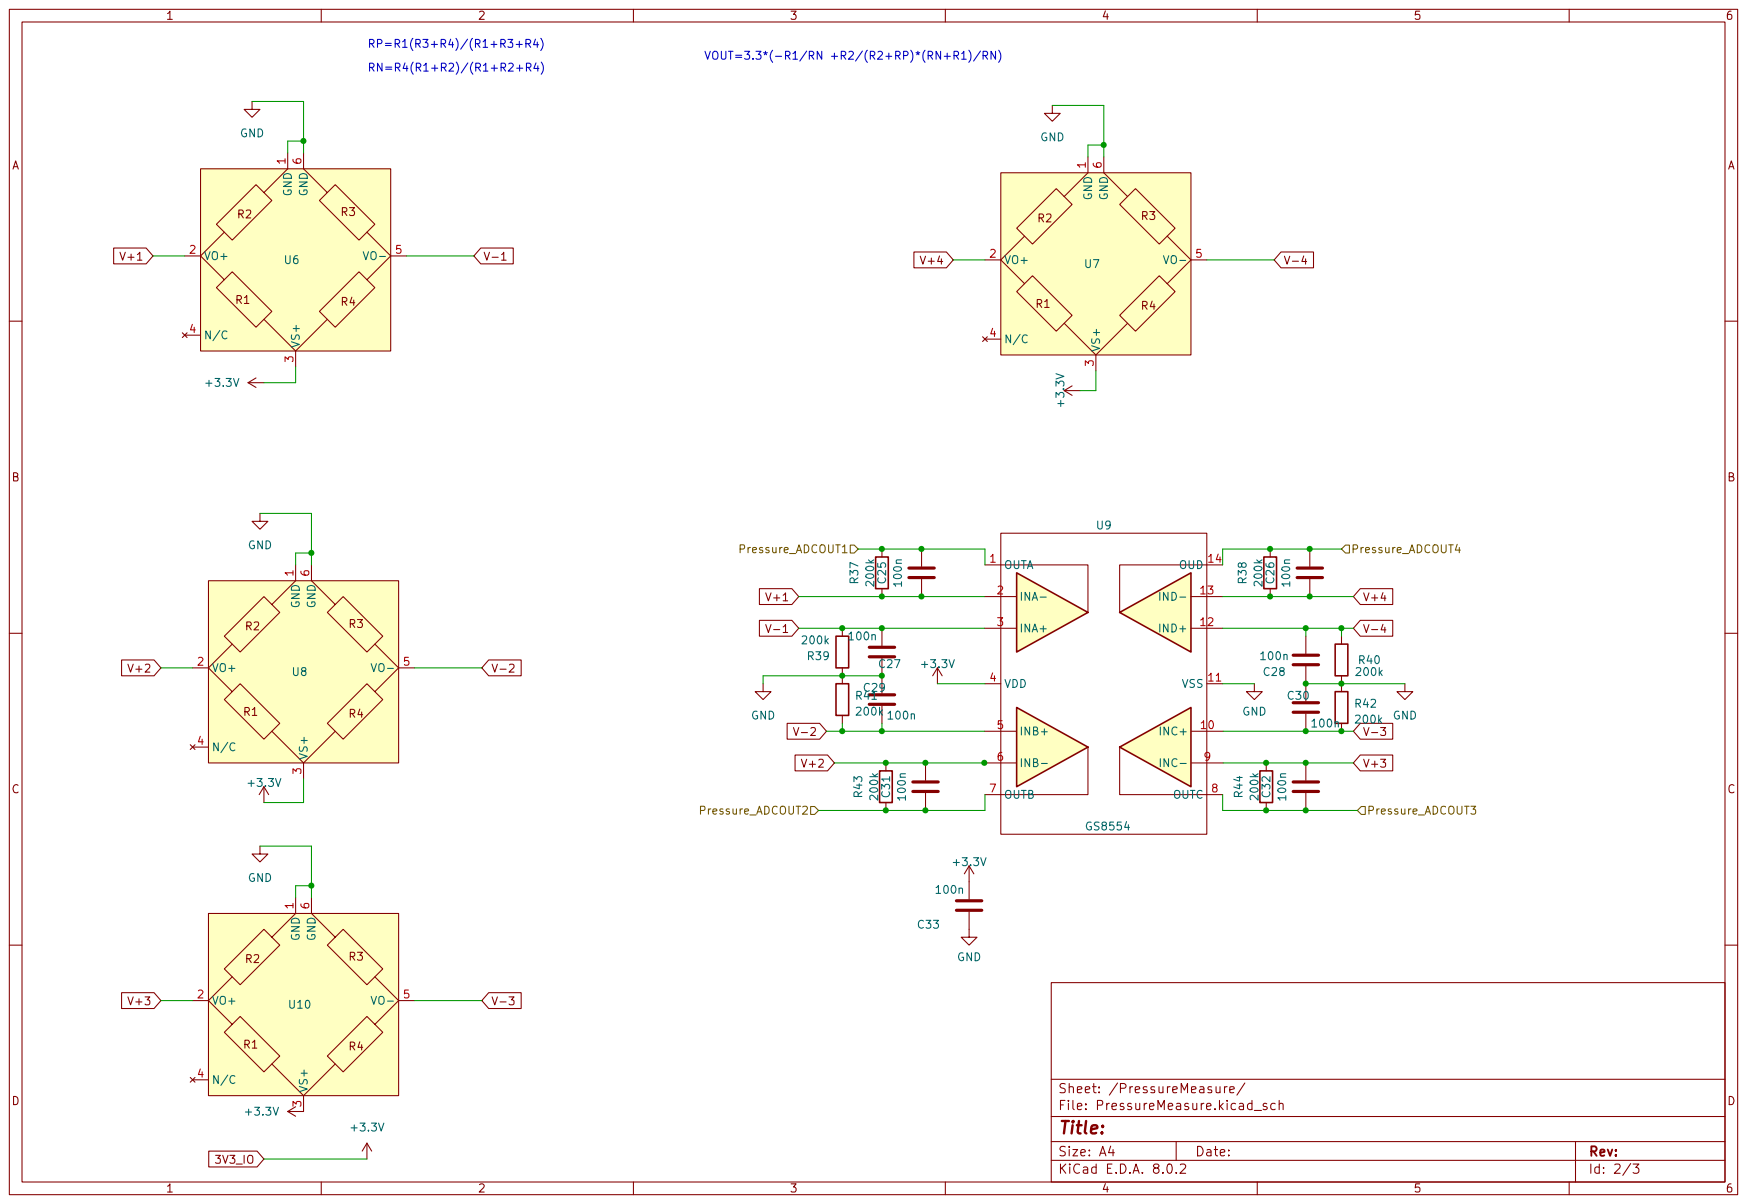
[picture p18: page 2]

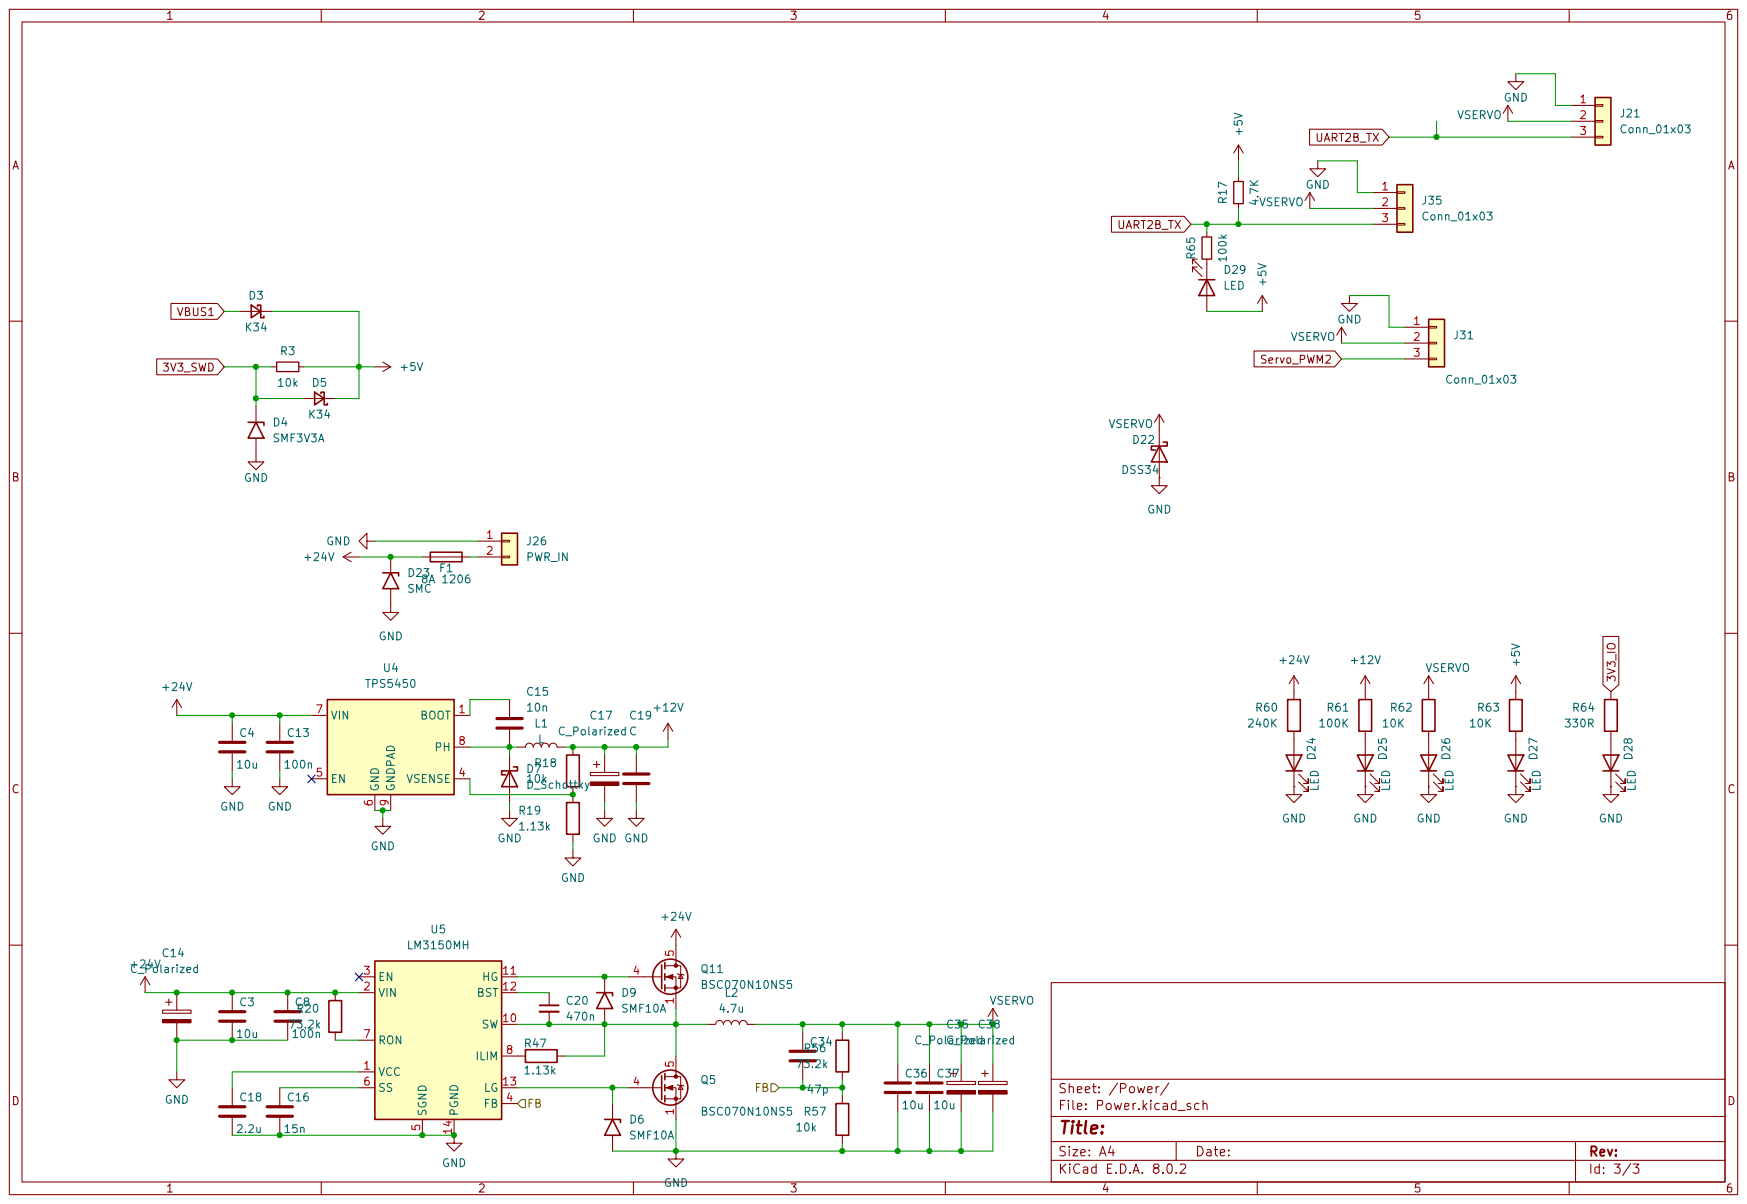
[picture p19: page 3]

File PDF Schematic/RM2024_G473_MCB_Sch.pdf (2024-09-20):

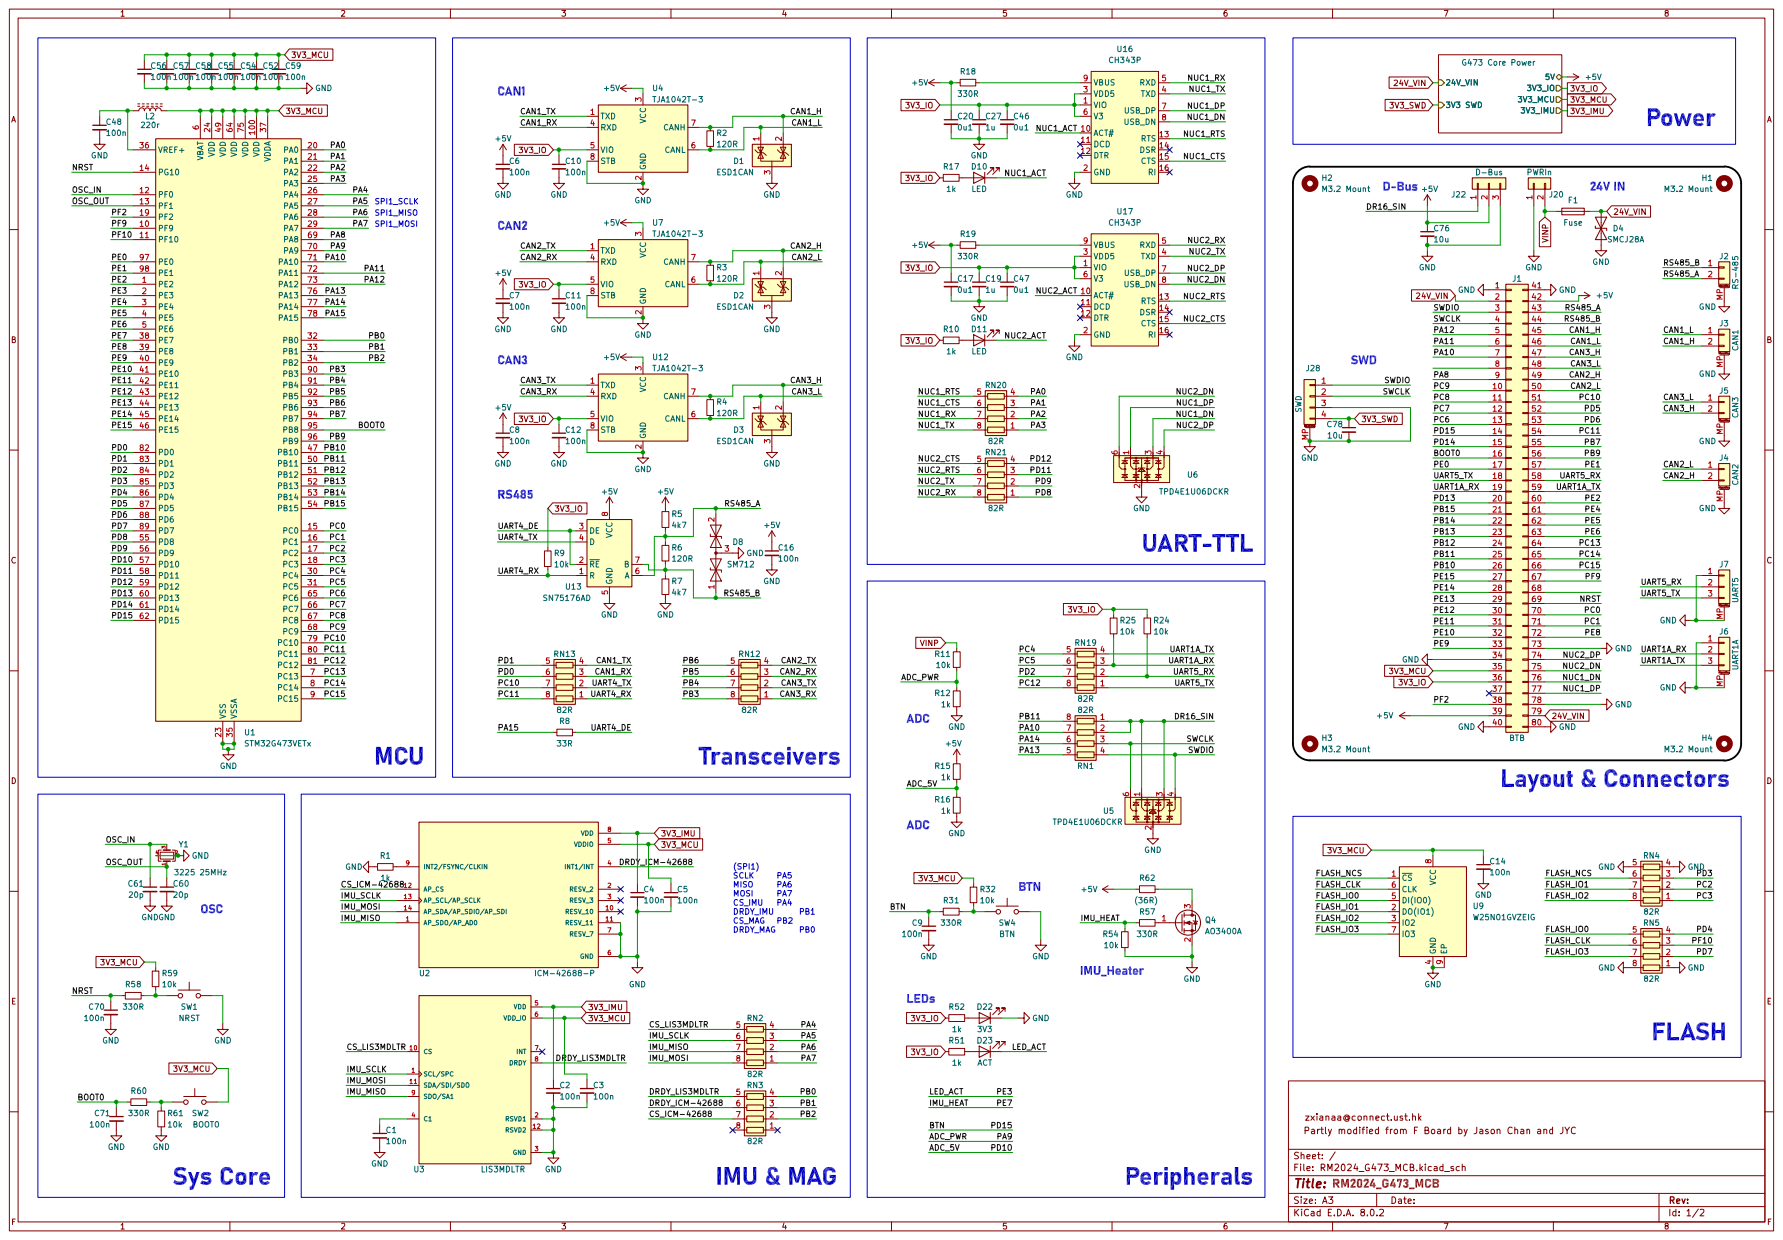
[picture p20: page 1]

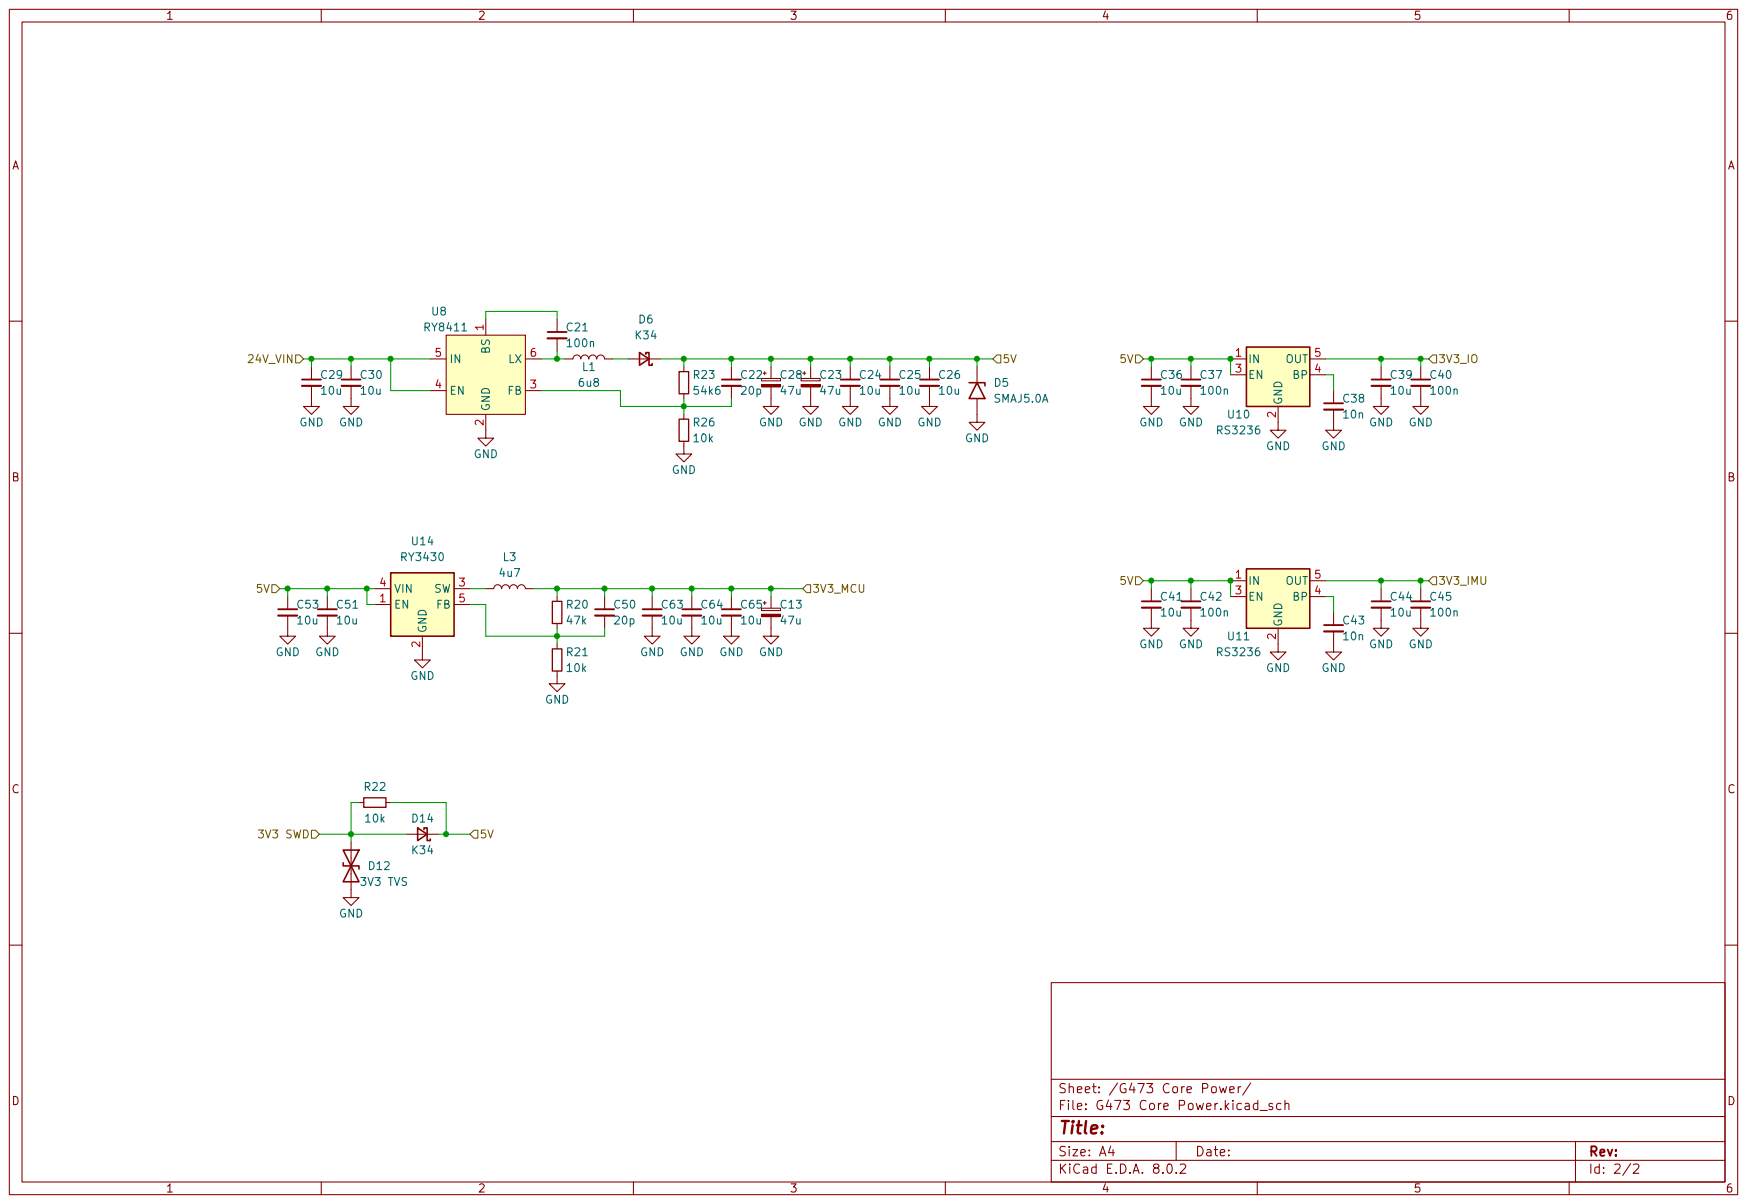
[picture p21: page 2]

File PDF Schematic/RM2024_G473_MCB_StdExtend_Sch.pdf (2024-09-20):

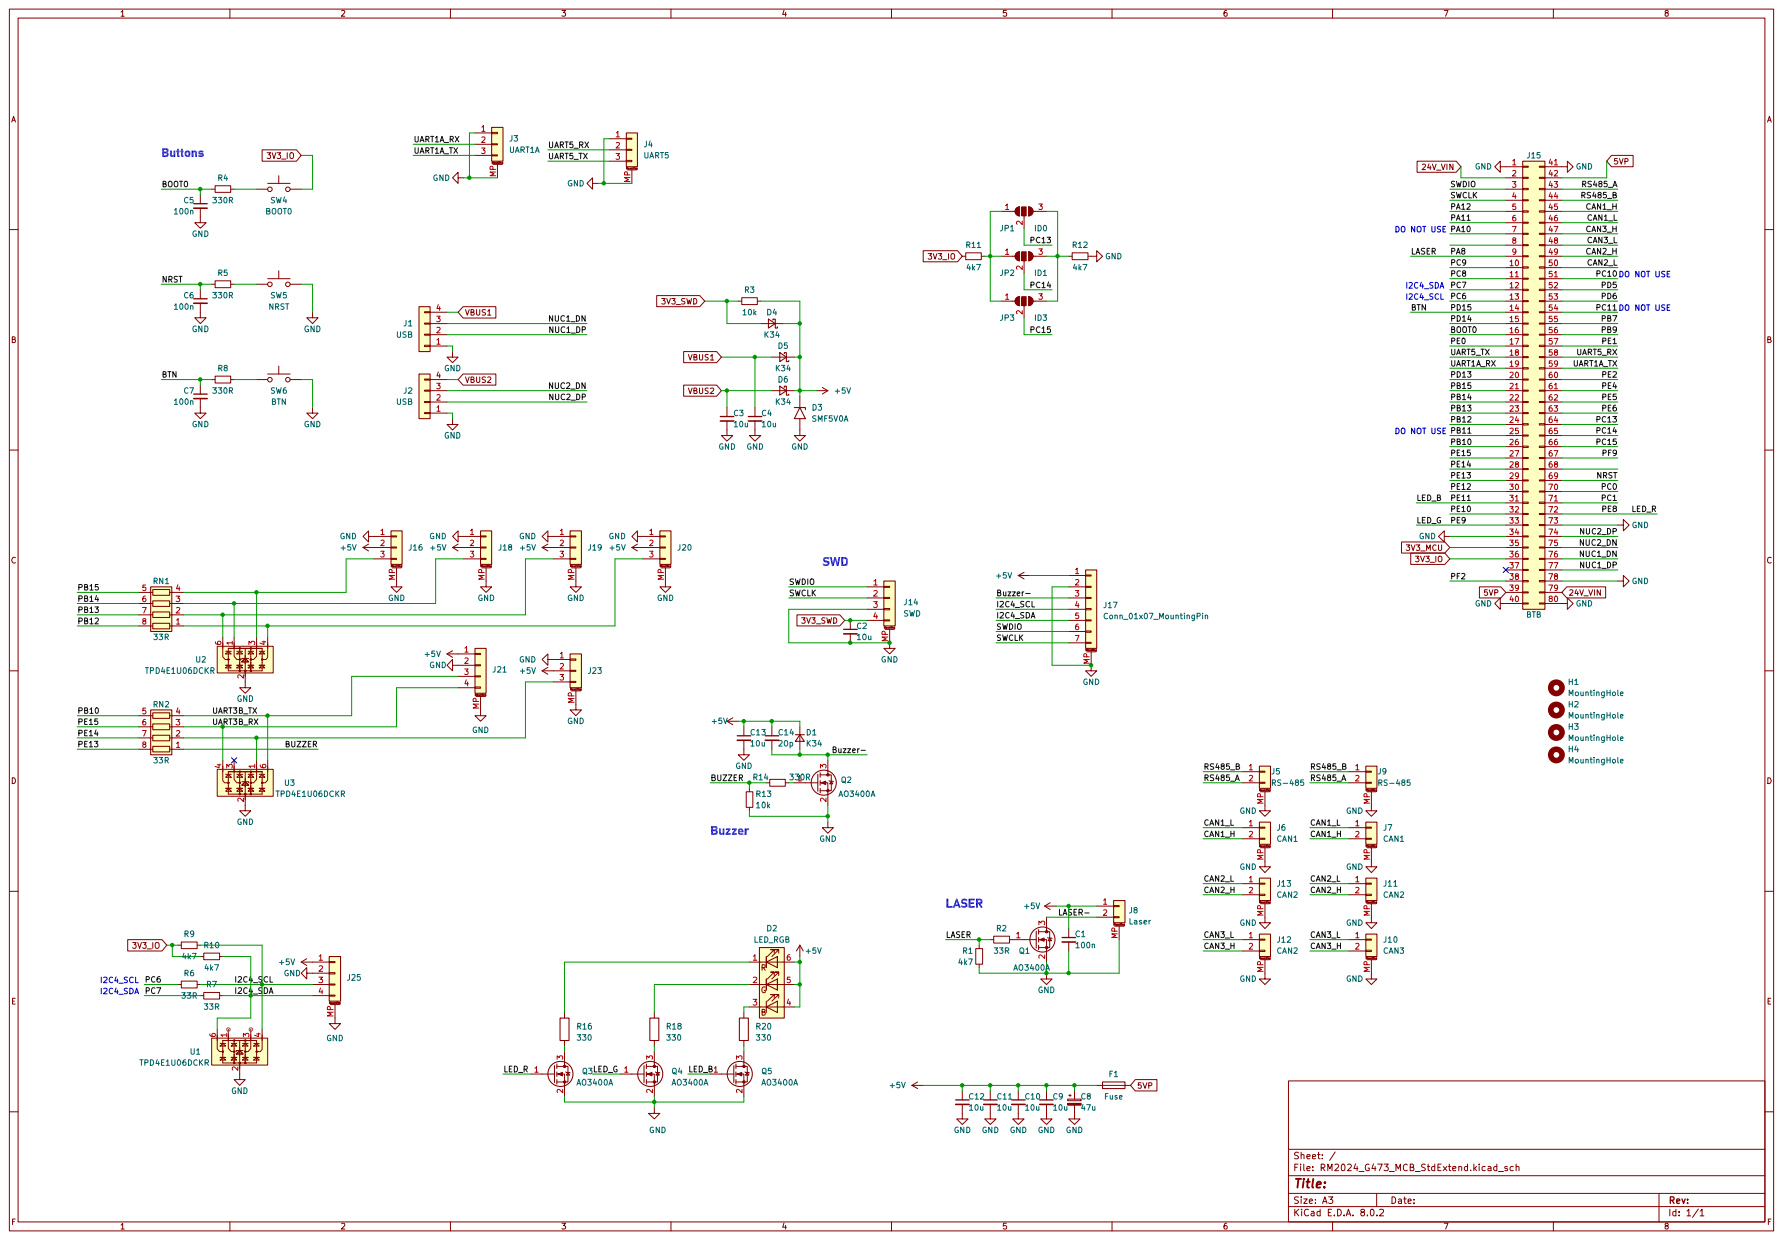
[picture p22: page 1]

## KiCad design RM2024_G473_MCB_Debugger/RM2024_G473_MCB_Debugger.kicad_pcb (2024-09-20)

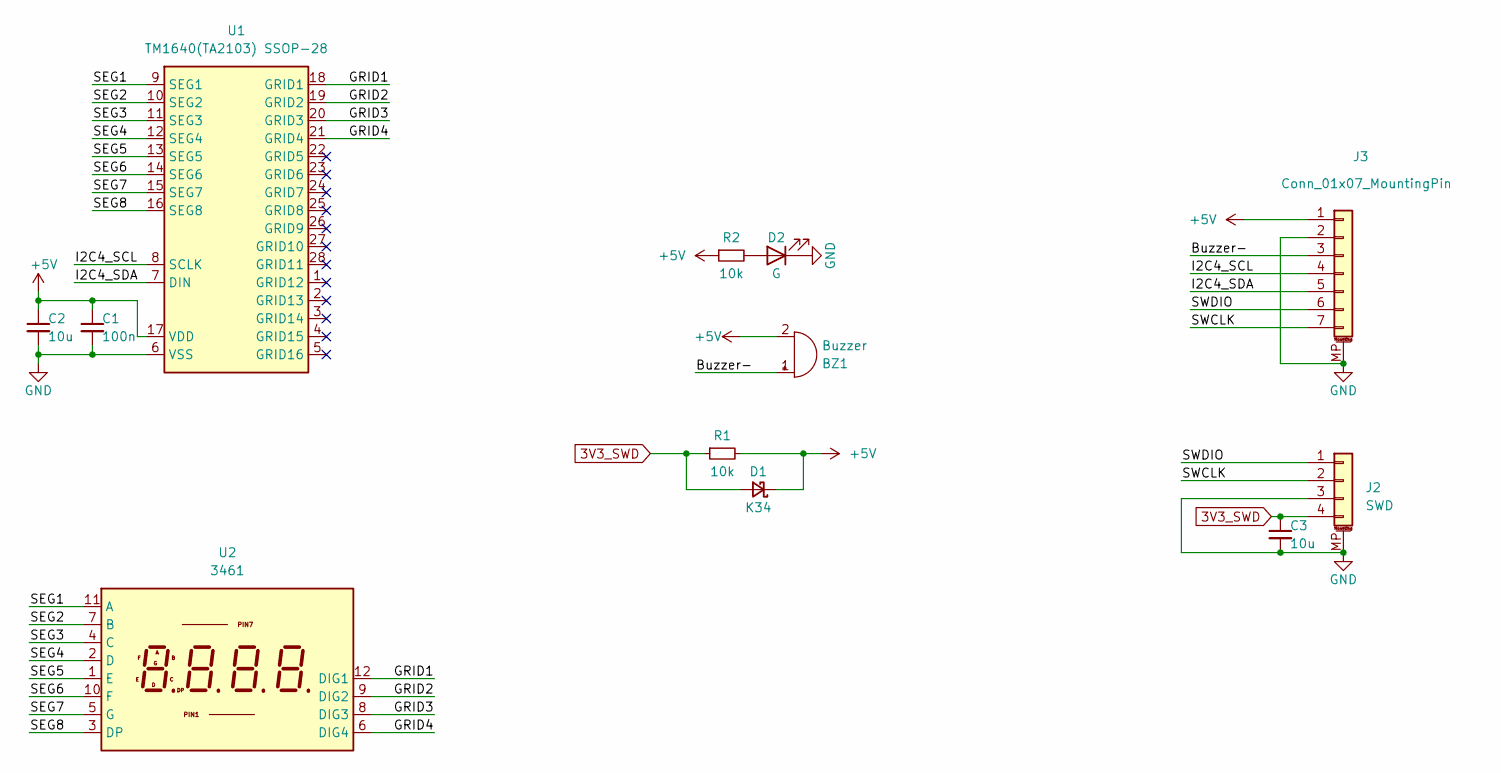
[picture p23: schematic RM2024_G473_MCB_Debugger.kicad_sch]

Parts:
BZ1: Buzzer; MLT-9032
C1: 100n; C_0603_1608Metric
C2, C3: 10u; C_0603_1608Metric
D1: K34; D_SMF
D2: G; LED_0603_1608Metric
J2: SWD; Molex_PicoBlade_53398-0471_1x04-1MP_P1.25mm_Vertical
J3: Conn_01x07_MountingPin; JST_GH_SM07B-GHS-TB_1x07-1MP_P1.25mm_Horizontal
R1, R2: 10k; R_0603_1608Metric
U1: TM1640(TA2103) SSOP-28; SSOP-28_3.9x9.9mm_P0.635mm
U2: 3461; LED-8888-3461

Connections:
3V3_SWD: C3.1, D1.2 (A), J2.4, R1.1
+5V: BZ1.2 (+), C1.1, C2.1, D1.1 (K), J3.1, R1.2, R2.1, U1.17 (VDD)
/Buzzer-: BZ1.1 (-), J3.3
/GRID1: U1.18 (GRID1), U2.12 (DIG1)
/GRID2: U1.19 (GRID2), U2.9 (DIG2)
/GRID3: U1.20 (GRID3), U2.8 (DIG3)
/GRID4: U1.21 (GRID4), U2.6 (DIG4)
/I2C4_SCL: J3.4, U1.8 (SCLK)
/I2C4_SDA: J3.5, U1.7 (DIN)
/SEG1: U1.9 (SEG1), U2.11 (A)
/SEG2: U1.10 (SEG2), U2.7 (B)
/SEG3: U1.11 (SEG3), U2.4 (C)
/SEG4: U1.12 (SEG4), U2.2 (D)
/SEG5: U1.13 (SEG5), U2.1 (E)
/SEG6: U1.14 (SEG6), U2.10 (F)
/SEG7: U1.15 (SEG7), U2.5 (G)
/SEG8: U1.16 (SEG8), U2.3 (DP)
/SWCLK: J2.2, J3.7
/SWDIO: J2.1, J3.6
GND: C1.2, C2.2, C3.2, D2.1 (K), J2.3, J2.MP (MountPin), J3.2, J3.MP (MountPin), U1.6 (VSS)
unnamed: D2.2 (A), R2.2

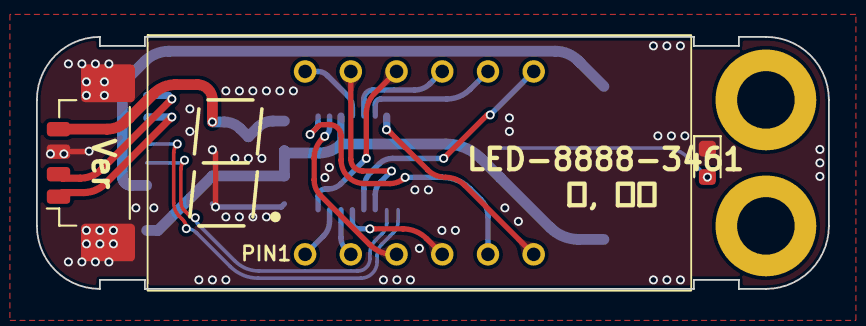
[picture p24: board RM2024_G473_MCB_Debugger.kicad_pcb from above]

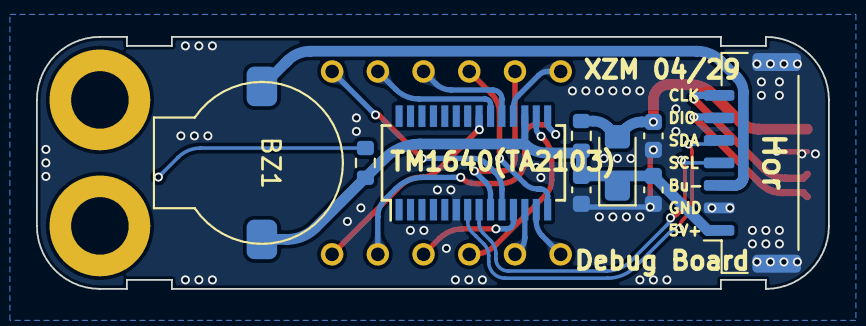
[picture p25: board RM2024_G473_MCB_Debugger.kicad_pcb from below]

Board: 2 copper layers, 44.0 x 14.0 mm, 12 parts (9 on the bottom side), 21 nets.

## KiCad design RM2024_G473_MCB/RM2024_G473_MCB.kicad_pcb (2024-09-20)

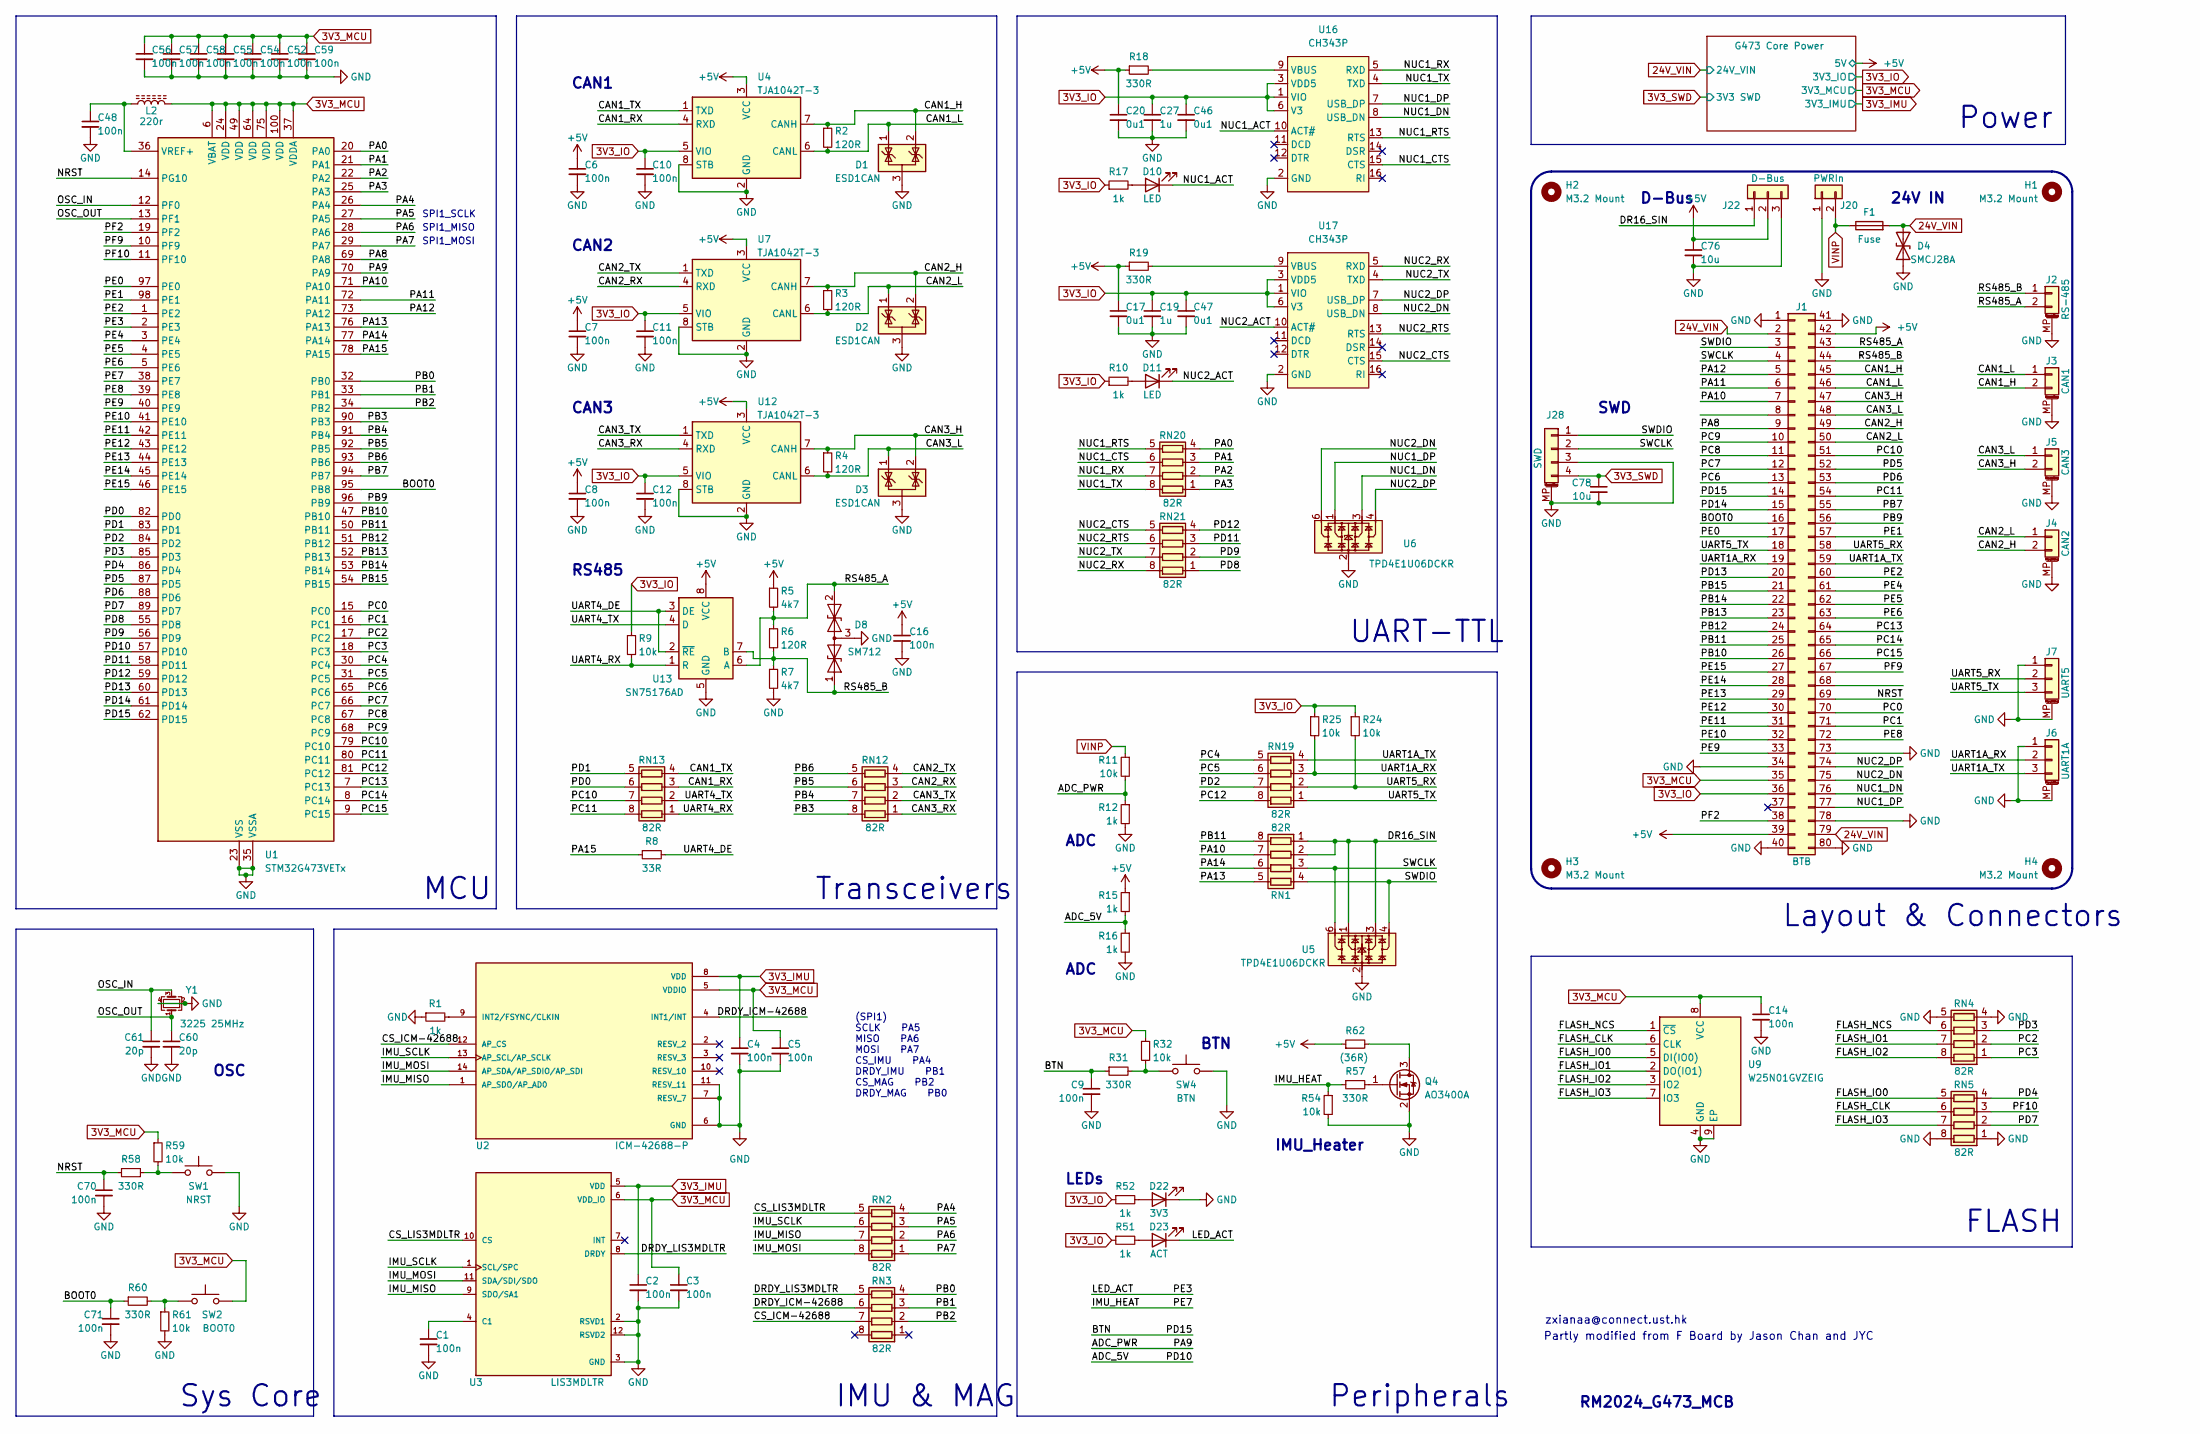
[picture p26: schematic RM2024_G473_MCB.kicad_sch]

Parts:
C1, C2, C3, C4, C5, C6, C7, C8, C9, C10, C11, C12, C14, C16, C48, C52, C54, C55, C56, C57, C58, C59, C70, C71: 100n; C_0603_1608Metric
C17, C20, C46, C47: 0u1; C_0603_1608Metric
C19, C27: 1u; C_0603_1608Metric
C60, C61: 20p; C_0603_1608Metric
C76, C78: 10u; C_0603_1608Metric
D1, D2, D3: ESD1CAN; SOT-23
D4: SMCJ28A; D_SMC
D8: SM712; SOT-23
D10, D11: LED; LED_0603_1608Metric
D22: 3V3; LED_0603_1608Metric
D23: ACT; LED_0603_1608Metric
F1: Fuse; Fuse_1206_3216Metric
H1, H2, H3, H4: M3.2 Mount; MountingHole_3.2mm_M3_DIN965_Pad
J1: BTB; BTB_P0.8mm_2x40pin_F
J2: RS-485; JST_GH_SM02B-GHS-TB_1x02-1MP_P1.25mm_Horizontal
J3: CAN1; JST_GH_SM02B-GHS-TB_1x02-1MP_P1.25mm_Horizontal
J4: CAN2; JST_GH_SM02B-GHS-TB_1x02-1MP_P1.25mm_Horizontal
J5: CAN3; JST_GH_SM02B-GHS-TB_1x02-1MP_P1.25mm_Horizontal
J6: UART1A; JST_GH_SM03B-GHS-TB_1x03-1MP_P1.25mm_Horizontal
J7: UART5; JST_GH_SM03B-GHS-TB_1x03-1MP_P1.25mm_Horizontal
J20: PWRIn; AMASS_XT30U-M_1x02_P5.0mm_Vertical
J22: D-Bus; PinHeader_1x03_P2.54mm_Vertical
J28: SWD; Molex_PicoBlade_53261-0471_1x04-1MP_P1.25mm_Horizontal
L2: 220r; L_0603_1608Metric
Q4: AO3400A; SOT-23
R1, R10, R12, R15, R16, R17, R51, R52: 1k; R_0603_1608Metric
R2, R3, R4, R6: 120R; R_0603_1608Metric
R5, R7: 4k7; R_0603_1608Metric
R8: 33R; R_0603_1608Metric
R9, R11, R24, R25, R32, R54, R59, R61: 10k; R_0603_1608Metric
R18, R19, R31, R57, R58, R60: 330R; R_0603_1608Metric
R62: (36R); R_1206_3216Metric
RN1, RN2, RN3, RN4, RN5, RN12, RN13, RN19, RN20, RN21: 82R; R_Array_Concave_4x0603
SW1: NRST; Panasonic_EVQPUL_EVQPUC
SW2: BOOT0; Panasonic_EVQPUL_EVQPUC
SW4: BTN; Panasonic_EVQPUL_EVQPUC
U1: STM32G473VETx; LQFP-100_14x14mm_P0.5mm
U2: ICM-42688-P; PQFN50P300X250X97-14N; PARTREV 1.2
U3: LIS3MDLTR; XDCR_LIS3MDLTR; PARTREV 6
U4, U7, U12: TJA1042T-3; SOIC-8_3.9x4.9mm_P1.27mm
U5, U6: TPD4E1U06DCKR; SOT-363_SC-70-6
U9: W25N01GVZEIG; WSON-8-1EP_8x6mm_P1.27mm_EP3.4x4.3mm
U13: SN75176AD; SOIC-8_3.9x4.9mm_P1.27mm
U16, U17: CH343P; TQFN-16-1EP_3x3mm_P0.5mm_EP1.6x1.6mm
Y1: 3225 25MHz; Crystal_SMD_3225-4Pin_3.2x2.5mm

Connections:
3V3_IMU: C2.1, C4.1, U2.8 (VDD), U3.5 (VDD); also elsewhere on the board
3V3_IO: C10.1, C11.1, C12.1, C19.1, C27.1, C46.1, C47.1, J1.36, R9.1, R10.1, R17.1, R24.1, R25.1, R51.1, R52.1, U4.5 (VIO), U7.5 (VIO), U12.5 (VIO), U16.1 (VIO), U16.3 (VDD5), U16.6 (V3), U17.1 (VIO), U17.3 (VDD5), U17.6 (V3); also elsewhere on the board
3V3_MCU: C3.1, C5.1, C14.1, C52.1, C54.1, C55.1, C56.1, C57.1, C58.1, C59.1, J1.35, L2.2, R32.1, R59.1, SW2.2, U1.6 (VBAT), U1.24 (VDD), U1.37 (VDDA), U1.49 (VDD), U1.64 (VDD), U1.75 (VDD), U1.100 (VDD), U2.5 (VDDIO), U3.6 (VDD_IO), U9.8 (VCC); also elsewhere on the board
3V3_SWD: C78.1, J28.4; also elsewhere on the board
24V_VIN: D4.1 (A1), F1.2, J1.2, J1.79; also elsewhere on the board
+5V: C6.1, C7.1, C8.1, C16.1, C17.1, C20.1, C76.1, J1.39, J1.42, J22.2, R5.1, R15.1, R18.1, R19.1, R62.1, U4.3 (VCC), U7.3 (VCC), U12.3 (VCC), U13.8 (VCC); also elsewhere on the board
/ADC_5V: R15.2, R16.1, U1.57 (PD10)
/ADC_PWR: R11.2, R12.1, U1.70 (PA9)
/BOOT0: C71.1, J1.16, R60.1, U1.95 (PB8)
/BTN: C9.1, J1.14, R31.1, U1.62 (PD15)
/CAN1_H: D1.2 (K), J1.45, J3.2, R2.1, U4.7 (CANH)
/CAN1_L: D1.1 (K), J1.46, J3.1, R2.2, U4.6 (CANL)
/CAN1_RX: RN13.3 (R3.1), U4.4 (RXD)
/CAN1_TX: RN13.4 (R4.1), U4.1 (TXD)
/CAN2_H: D2.2 (K), J1.49, J4.2, R3.1, U7.7 (CANH)
/CAN2_L: D2.1 (K), J1.50, J4.1, R3.2, U7.6 (CANL)
/CAN2_RX: RN12.3 (R3.1), U7.4 (RXD)
/CAN2_TX: RN12.4 (R4.1), U7.1 (TXD)
/CAN3_H: D3.2 (K), J1.47, J5.2, R4.1, U12.7 (CANH)
/CAN3_L: D3.1 (K), J1.48, J5.1, R4.2, U12.6 (CANL)
/CAN3_RX: RN12.1 (R1.1), U12.4 (RXD)
/CAN3_TX: RN12.2 (R2.1), U12.1 (TXD)
/CS_ICM-42688: RN3.7 (R2.2), U2.12 (AP_CS)
/CS_LIS3MDLTR: RN2.5 (R4.2), U3.10 (CS)
/DR16_SIN: J22.1, RN1.1 (R1.1), RN1.2 (R2.1), U5.1, U5.3
/DRDY_ICM-42688: RN3.6 (R3.2), U2.4 (INT1/INT)
/DRDY_LIS3MDLTR: RN3.5 (R4.2), U3.8 (DRDY)
/FLASH_CLK: RN5.6 (R3.2), U9.6 (CLK)
/FLASH_IO0: RN5.5 (R4.2), U9.5 (DI(IO0))
/FLASH_IO1: RN4.7 (R2.2), U9.2 (DO(IO1))
/FLASH_IO2: RN4.8 (R1.2), U9.3 (IO2)
/FLASH_IO3: RN5.7 (R2.2), U9.7 (IO3)
/FLASH_NCS: RN4.6 (R3.2), U9.1 (~CS)
/IMU_HEAT: R54.1, R57.1, U1.38 (PE7)
/IMU_MISO: RN2.7 (R2.2), U2.1 (AP_SDO/AP_AD0), U3.9 (SDO/SA1)
/IMU_MOSI: RN2.8 (R1.2), U2.14 (AP_SDA/AP_SDIO/AP_SDI), U3.11 (SDA/SDI/SDO)
/IMU_SCLK: RN2.6 (R3.2), U2.13 (AP_SCL/AP_SCLK), U3.1 (SCL/SPC)
/LED_ACT: D23.1 (K), U1.2 (PE3)
/NRST: C70.1, J1.69, R58.1, U1.14 (PG10)
/NUC1_ACT: D10.1 (K), U16.10 (ACT#)
/NUC1_CTS: RN20.6 (R3.2), U16.15 (CTS)
/NUC1_DN: J1.76, U6.3, U16.8 (USB_DN)
/NUC1_DP: J1.77, U6.1, U16.7 (USB_DP)
/NUC1_RTS: RN20.5 (R4.2), U16.13 (RTS)
/NUC1_RX: RN20.7 (R2.2), U16.5 (RXD)
/NUC1_TX: RN20.8 (R1.2), U16.4 (TXD)
/NUC2_ACT: D11.1 (K), U17.10 (ACT#)
/NUC2_CTS: RN21.5 (R4.2), U17.15 (CTS)
/NUC2_DN: J1.75, U6.6, U17.8 (USB_DN)
/NUC2_DP: J1.74, U6.4, U17.7 (USB_DP)
/NUC2_RTS: RN21.6 (R3.2), U17.13 (RTS)
/NUC2_RX: RN21.8 (R1.2), U17.5 (RXD)
/NUC2_TX: RN21.7 (R2.2), U17.4 (TXD)
/OSC_IN: C61.1, U1.12 (PF0), Y1.3
/OSC_OUT: C60.1, U1.13 (PF1), Y1.1
/PA0: RN20.4 (R4.1), U1.20 (PA0)
/PA1: RN20.3 (R3.1), U1.21 (PA1)
/PA2: RN20.2 (R2.1), U1.22 (PA2)
/PA3: RN20.1 (R1.1), U1.25 (PA3)
/PA4: RN2.4 (R4.1), U1.26 (PA4)
/PA5: RN2.3 (R3.1), U1.27 (PA5)
/PA6: RN2.2 (R2.1), U1.28 (PA6)
/PA7: RN2.1 (R1.1), U1.29 (PA7)
/PA8: J1.9, U1.69 (PA8)
/PA10: J1.7, RN1.7 (R2.2), U1.71 (PA10)
/PA11: J1.6, U1.72 (PA11)
/PA12: J1.5, U1.73 (PA12)
/PA13: RN1.5 (R4.2), U1.76 (PA13)
/PA14: RN1.6 (R3.2), U1.77 (PA14)
/PA15: R8.1, U1.78 (PA15)
/PB0: RN3.4 (R4.1), U1.32 (PB0)
/PB1: RN3.3 (R3.1), U1.33 (PB1)
/PB2: RN3.2 (R2.1), U1.34 (PB2)
/PB3: RN12.8 (R1.2), U1.90 (PB3)
/PB4: RN12.7 (R2.2), U1.91 (PB4)
/PB5: RN12.6 (R3.2), U1.92 (PB5)
/PB6: RN12.5 (R4.2), U1.93 (PB6)
/PB7: J1.55, U1.94 (PB7)
/PB9: J1.56, U1.96 (PB9)
/PB10: J1.26, U1.47 (PB10)
/PB11: J1.25, RN1.8 (R1.2), U1.50 (PB11)
/PB12: J1.24, U1.51 (PB12)
/PB13: J1.23, U1.52 (PB13)
/PB14: J1.22, U1.53 (PB14)
/PB15: J1.21, U1.54 (PB15)
/PC0: J1.70, U1.15 (PC0)
/PC1: J1.71, U1.16 (PC1)
/PC2: RN4.2 (R2.1), U1.17 (PC2)
/PC3: RN4.1 (R1.1), U1.18 (PC3)
/PC4: RN19.5 (R4.2), U1.30 (PC4)
/PC5: RN19.6 (R3.2), U1.31 (PC5)
/PC6: J1.13, U1.65 (PC6)
/PC7: J1.12, U1.66 (PC7)
/PC8: J1.11, U1.67 (PC8)
/PC9: J1.10, U1.68 (PC9)
/PC10: J1.51, RN13.7 (R2.2), U1.79 (PC10)
/PC11: J1.54, RN13.8 (R1.2), U1.80 (PC11)
/PC12: RN19.8 (R1.2), U1.81 (PC12)
/PC13: J1.64, U1.7 (PC13)
/PC14: J1.65, U1.8 (PC14)
/PC15: J1.66, U1.9 (PC15)
/PD0: RN13.6 (R3.2), U1.82 (PD0)
/PD1: RN13.5 (R4.2), U1.83 (PD1)
/PD2: RN19.7 (R2.2), U1.84 (PD2)
/PD3: RN4.3 (R3.1), U1.85 (PD3)
/PD4: RN5.4 (R4.1), U1.86 (PD4)
/PD5: J1.52, U1.87 (PD5)
/PD6: J1.53, U1.88 (PD6)
/PD7: RN5.2 (R2.1), U1.89 (PD7)
/PD8: RN21.1 (R1.1), U1.55 (PD8)
/PD9: RN21.2 (R2.1), U1.56 (PD9)
/PD11: RN21.3 (R3.1), U1.58 (PD11)
/PD12: RN21.4 (R4.1), U1.59 (PD12)
/PD13: J1.20, U1.60 (PD13)
/PD14: J1.15, U1.61 (PD14)
/PE0: J1.17, U1.97 (PE0)
/PE1: J1.57, U1.98 (PE1)
/PE2: J1.60, U1.1 (PE2)
/PE4: J1.61, U1.3 (PE4)
/PE5: J1.62, U1.4 (PE5)
/PE6: J1.63, U1.5 (PE6)
/PE8: J1.72, U1.39 (PE8)
/PE9: J1.33, U1.40 (PE9)
/PE10: J1.32, U1.41 (PE10)
/PE11: J1.31, U1.42 (PE11)
/PE12: J1.30, U1.43 (PE12)
/PE13: J1.29, U1.44 (PE13)
/PE14: J1.28, U1.45 (PE14)
/PE15: J1.27, U1.46 (PE15)
/PF2: J1.38, U1.19 (PF2)
/PF9: J1.67, U1.10 (PF9)
/PF10: RN5.3 (R3.1), U1.11 (PF10)
/RS485_A: D8.2 (A2), J1.43, J2.2, R5.2, R6.1, U13.6 (A)
/RS485_B: D8.1 (A1), J1.44, J2.1, R6.2, R7.1, U13.7 (B)
/SWCLK: J1.4, J28.2, RN1.3 (R3.1), U5.6
/SWDIO: J1.3, J28.1, RN1.4 (R4.1), U5.4
/UART1A_RX: J1.19, J6.2, R25.2, RN19.3 (R3.1)
/UART1A_TX: J1.59, J6.3, RN19.4 (R4.1)
/UART4_DE: R8.2, U13.2 (~RE), U13.3 (DE)
/UART4_RX: R9.2, RN13.1 (R1.1), U13.1 (R)
/UART4_TX: RN13.2 (R2.1), U13.4 (D)
/UART5_RX: J1.58, J7.2, R24.2, RN19.2 (R2.1)
/UART5_TX: J1.18, J7.3, RN19.1 (R1.1)
GND: C1.2, C2.2, C3.2, C4.2, C5.2, C6.2, C7.2, C8.2, C9.2, C10.2, C11.2, C12.2, C14.2, C16.2, C17.2, C19.2, C20.2, C27.2, C46.2, C47.2, C48.2, C52.2, C54.2, C55.2, C56.2, C57.2, C58.2, C59.2, C60.2, C61.2, C70.2, C71.2, C76.2, C78.2, D1.3 (A), D2.3 (A), D3.3 (A), D4.2 (A2), D8.3 (common), D22.1 (K), J1.1, J1.34, J1.40, J1.41, J1.73, J1.78, J1.80, J2.MP (MountPin), J3.MP (MountPin), J4.MP (MountPin), J5.MP (MountPin), J6.1, J6.MP (MountPin), J7.1, J7.MP (MountPin), J20.1, J22.3, J28.3, J28.MP (MountPin), Q4.2 (S), R1.1, R7.2, R12.2, R16.2, R54.2, R61.2, RN4.4 (R4.1), RN4.5 (R4.2), RN5.1 (R1.1), RN5.8 (R1.2), SW1.2, SW4.2, U1.23 (VSS), U1.35 (VSSA), U1.48 (VSS), U1.63 (VSS), U1.74 (VSS), U1.99 (VSS), U2.6 (GND), U2.7 (RESV_7), U2.11 (RESV_11), U3.2 (RSVD1), U3.3 (GND), U3.12 (RSVD2), U4.2 (GND), U4.8 (STB), U5.2, U6.2, U7.2 (GND), U7.8 (STB), U9.4 (GND), U9.9 (EP), U12.2 (GND), U12.8 (STB), U13.5 (GND), U16.2 (GND), U16.17 (GND), U17.2 (GND), U17.17 (GND), Y1.2, Y1.4; also elsewhere on the board
unnamed: D10.2 (A), R17.2
unnamed: D11.2 (A), R10.2
unnamed: D22.2 (A), R52.2
unnamed: D23.2 (A), R51.2
unnamed: Q4.3 (D), R62.2
unnamed: Q4.1 (G), R57.2
unnamed: R31.2, R32.2, SW4.1
unnamed: R58.2, R59.2, SW1.1
unnamed: R60.2, R61.1, SW2.1
unnamed: C48.1, L2.1, U1.36 (VREF+)
unnamed: R1.2, U2.9 (INT2/FSYNC/CLKIN)
unnamed: C1.1, U3.4 (C1)
unnamed: R18.2, U16.9 (VBUS)
unnamed: R19.2, U17.9 (VBUS)
VINP: F1.1, J20.2, R11.1

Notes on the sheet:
SPI1_MOSI
ADC
(SPI1) SCLK PA5 MISO PA6 MOSI PA7 CS_IMU PA4 DRDY_IMU PB1 CS_MAG PB2 DRDY_MAG PB0
BTN
FLASH
OSC
IMU & MAG
Power
CAN1
24V IN
IMU_Heater
Layout & Connectors
Transceivers
Partly modified from F Board by Jason Chan and JYC
CAN3
RS485
SWD
SPI1_SCLK
Peripherals
RM2024_G473_MCB
MCU
Sys Core
SPI1_MISO
UART-TTL
LEDs
D-Bus
zxianaa@connect.ust.hk
CAN2

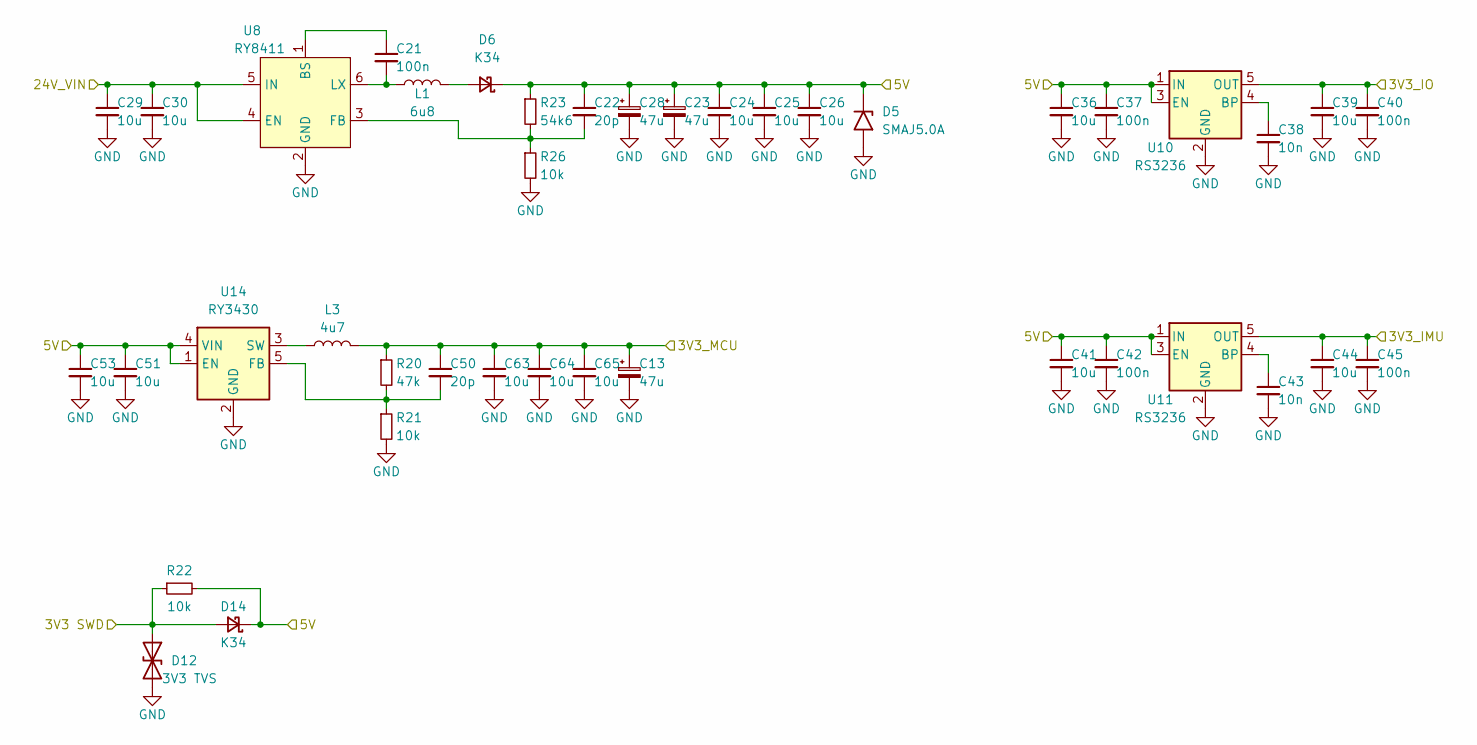
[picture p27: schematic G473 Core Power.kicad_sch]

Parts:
C13, C23, C28: 47u; CP_EIA-3216-18_Kemet-A_Pad1.58x1.35mm_HandSolder
C21, C37, C40, C42, C45: 100n; C_0603_1608Metric
C22, C50: 20p; C_0603_1608Metric
C24, C25, C26, C29, C30: 10u; C_1206_3216Metric
C36, C39, C41, C44, C51, C53, C63, C64, C65: 10u; C_0603_1608Metric
C38, C43: 10n; C_0603_1608Metric
D5: SMAJ5.0A; D_SMA
D6, D14: K34; D_SMF
D12: 3V3 TVS; D_SMF
L1: 6u8; L_Sunlord_MWSA0402S
L3: 4u7; L_Sunlord_MWSA0402S
R20: 47k; R_0603_1608Metric
R21, R22, R26: 10k; R_0603_1608Metric
R23: 54k6; R_0603_1608Metric
U8: RY8411; SOT-23-6
U10, U11: RS3236; SOT-23-5
U14: RY3430; SOT-23-5

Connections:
3V3_IMU: C44.1, C45.1, U11.5 (OUT); also elsewhere on the board
3V3_IO: C39.1, C40.1, U10.5 (OUT); also elsewhere on the board
3V3_MCU: C13.1, C50.1, C63.1, C64.1, C65.1, L3.2, R20.1; also elsewhere on the board
3V3_SWD: D12.1 (A1), D14.2 (A), R22.1; also elsewhere on the board
24V_VIN: C29.1, C30.1, U8.4 (EN), U8.5 (IN); also elsewhere on the board
+5V: C22.1, C23.1, C24.1, C25.1, C26.1, C28.1, C36.1, C37.1, C41.1, C42.1, C51.1, C53.1, D5.1 (A1), D6.1 (K), D14.1 (K), R22.2, R23.1, U10.1 (IN), U10.3 (EN), U11.1 (IN), U11.3 (EN), U14.1 (EN), U14.4 (VIN); also elsewhere on the board
GND: C13.2, C23.2, C24.2, C25.2, C26.2, C28.2, C29.2, C30.2, C36.2, C37.2, C38.2, C39.2, C40.2, C41.2, C42.2, C43.2, C44.2, C45.2, C51.2, C53.2, C63.2, C64.2, C65.2, D5.2 (A2), D12.2 (A2), R21.2, R26.2, U8.2 (GND), U10.2 (GND), U11.2 (GND), U14.2 (GND); also elsewhere on the board
unnamed: D6.2 (A), L1.2
unnamed: C21.1, U8.1 (BS)
unnamed: C22.2, R23.2, R26.1, U8.3 (FB)
unnamed: C21.2, L1.1, U8.6 (LX)
unnamed: C38.1, U10.4 (BP)
unnamed: C43.1, U11.4 (BP)
unnamed: C50.2, R20.2, R21.1, U14.5 (FB)
unnamed: L3.1, U14.3 (SW)

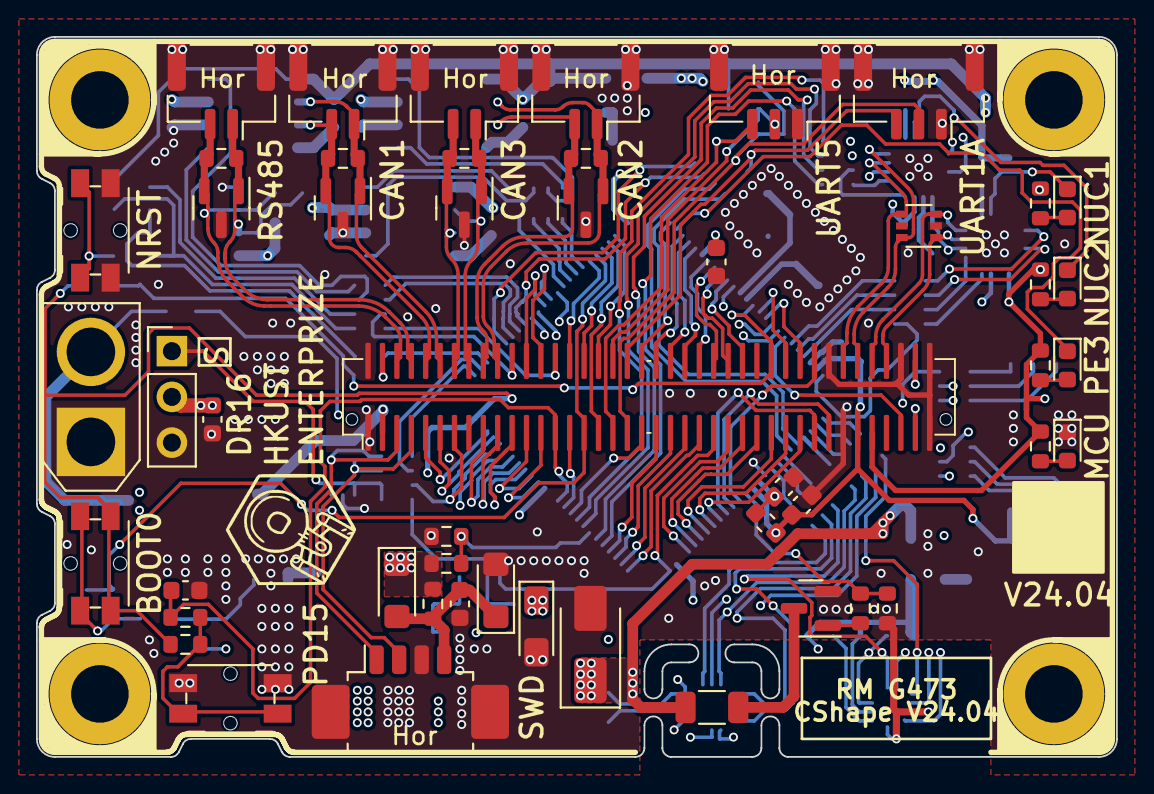
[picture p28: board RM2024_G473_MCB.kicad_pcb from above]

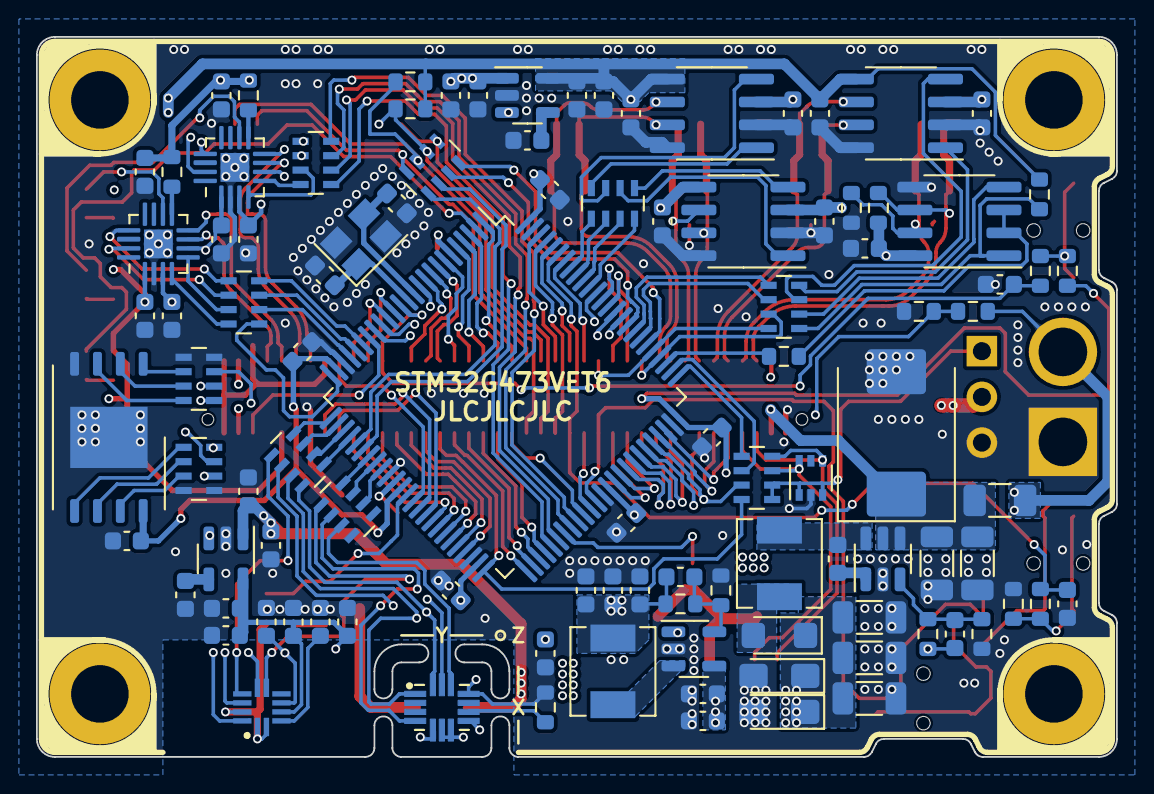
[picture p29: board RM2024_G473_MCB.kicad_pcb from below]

Board: 4 copper layers, 60.0 x 40.0 mm, 157 parts (103 on the bottom side), 167 nets.

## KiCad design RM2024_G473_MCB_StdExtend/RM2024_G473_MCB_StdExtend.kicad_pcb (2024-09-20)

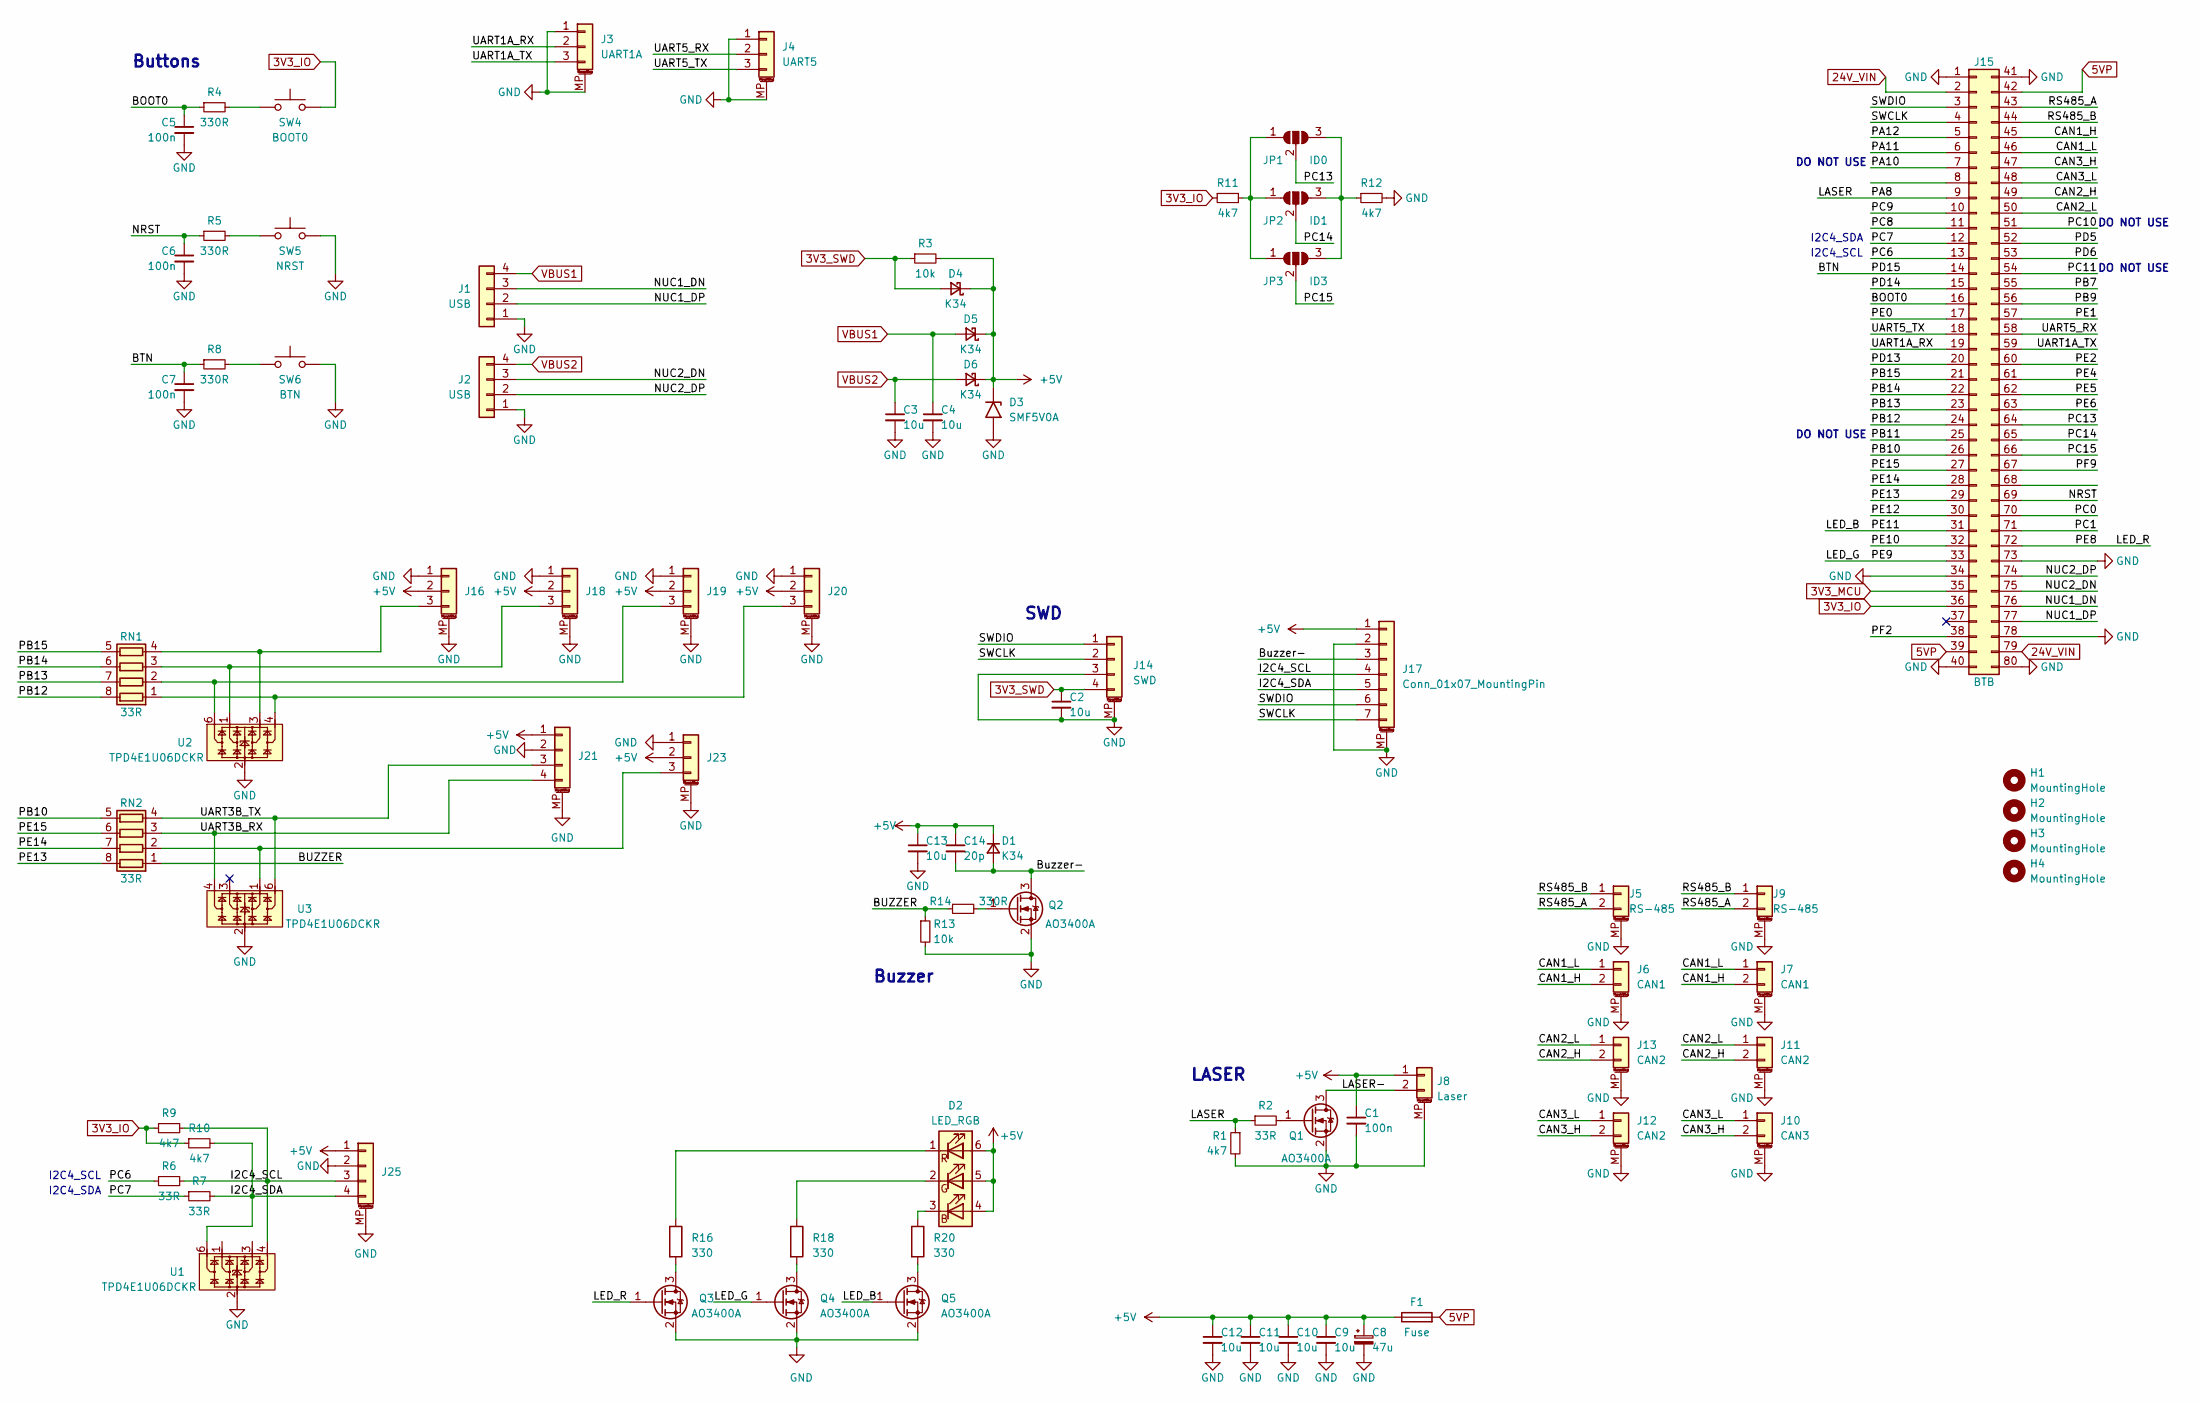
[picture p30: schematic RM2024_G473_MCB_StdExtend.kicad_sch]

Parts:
C1, C5, C6, C7: 100n; C_0603_1608Metric
C2, C3, C4, C9, C10, C11, C12, C13: 10u; C_0603_1608Metric
C8: 47u; CP_EIA-3216-18_Kemet-A_Pad1.58x1.35mm_HandSolder
C14: 20p; C_0603_1608Metric
D1, D4, D5, D6: K34; D_SMF
D2: LED_RGB; LED_RGB_5050-6
D3: SMF5V0A; D_SMF
F1: Fuse; Fuse_1206_3216Metric
H1, H2, H3, H4: MountingHole; MountingHole_3.2mm_M3_DIN965_Pad
J1, J2: USB; JST_PH_B4B-PH-K_1x04_P2.00mm_Vertical
J3: UART1A; JST_GH_BM03B-GHS-TBT_1x03-1MP_P1.25mm_Vertical
J4: UART5; JST_GH_BM03B-GHS-TBT_1x03-1MP_P1.25mm_Vertical
J5, J9: RS-485; JST_GH_BM02B-GHS-TBT_1x02-1MP_P1.25mm_Vertical
J6, J7: CAN1; JST_GH_BM02B-GHS-TBT_1x02-1MP_P1.25mm_Vertical
J8: Laser; Molex_PicoBlade_53398-0271_1x02-1MP_P1.25mm_Vertical
J10: CAN3; JST_GH_BM02B-GHS-TBT_1x02-1MP_P1.25mm_Vertical
J11, J12, J13: CAN2; JST_GH_BM02B-GHS-TBT_1x02-1MP_P1.25mm_Vertical
J14: SWD; Molex_PicoBlade_53398-0471_1x04-1MP_P1.25mm_Vertical
J15: BTB; BTB_P0.8mm_2x40pin_M
J16, J18, J19, J20, J23: Conn_01x03_MountingPin; JST_GH_BM03B-GHS-TBT_1x03-1MP_P1.25mm_Vertical
J17: Conn_01x07_MountingPin; JST_GH_BM07B-GHS-TBT_1x07-1MP_P1.25mm_Vertical
J21, J25: Conn_01x04_MountingPin; JST_GH_BM04B-GHS-TBT_1x04-1MP_P1.25mm_Vertical
JP1: ID0; SolderJumper-3_P1.3mm_Open_RoundedPad1.0x1.5mm_NumberLabels
JP2: ID1; SolderJumper-3_P1.3mm_Open_RoundedPad1.0x1.5mm_NumberLabels
JP3: ID3; SolderJumper-3_P1.3mm_Open_RoundedPad1.0x1.5mm_NumberLabels
Q1, Q2, Q3, Q4, Q5: AO3400A; SOT-23
R1, R9, R10, R11, R12: 4k7; R_0603_1608Metric
R2, R6, R7: 33R; R_0603_1608Metric
R3, R13: 10k; R_0603_1608Metric
R4, R5, R8, R14: 330R; R_0603_1608Metric
R16, R18, R20: 330; R_0603_1608Metric
RN1, RN2: 33R; R_Array_Concave_4x0603
SW4: BOOT0; SW_SPST_PTS810
SW5: NRST; SW_SPST_PTS810
SW6: BTN; SW_SPST_PTS810
U1, U2, U3: TPD4E1U06DCKR; SOT-363_SC-70-6

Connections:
3V3_IO: J15.36, R9.1, R10.1, R11.1, SW4.2
3V3_MCU: J15.35
3V3_SWD: C2.1, D4.2 (A), J14.4, R3.1
5VP: F1.2, J15.39, J15.42
24V_VIN: J15.2, J15.79
+5V: C1.1, C8.1, C9.1, C10.1, C11.1, C12.1, C13.1, C14.1, D1.1 (K), D2.4 (BA), D2.5 (GA), D2.6 (RA), D3.1 (A1), D4.1 (K), D5.1 (K), D6.1 (K), F1.1, J8.1, J16.2, J17.1, J18.2, J19.2, J20.2, J21.1, J23.2, J25.1, R3.2
/BOOT0: C5.1, J15.16, R4.1
/BTN: C7.1, J15.14, R8.1
/BUZZER: R13.1, R14.1, RN2.1 (R1.1)
/Buzzer-: C14.2, D1.2 (A), J17.3, Q2.3 (D)
/CAN1_H: J6.2, J7.2, J15.45
/CAN1_L: J6.1, J7.1, J15.46
/CAN2_H: J11.2, J13.2, J15.49
/CAN2_L: J11.1, J13.1, J15.50
/CAN3_H: J10.2, J12.2, J15.47
/CAN3_L: J10.1, J12.1, J15.48
/I2C4_SCL: J17.4, J25.3, R6.2, R9.2, U1.4
/I2C4_SDA: J17.5, J25.4, R7.2, R10.2, U1.6
/LASER: J15.9, R1.1, R2.1
/LASER-: J8.2, Q1.3 (D)
/LED_B: J15.31, Q5.1 (G)
/LED_G: J15.33, Q4.1 (G)
/LED_R: J15.72, Q3.1 (G)
/NRST: C6.1, J15.69, R5.1
/NUC1_DN: J1.3, J15.76
/NUC1_DP: J1.2, J15.77
/NUC2_DN: J2.3, J15.75
/NUC2_DP: J2.2, J15.74
/PA10: J15.7
/PA11: J15.6
/PA12: J15.5
/PB7: J15.55
/PB9: J15.56
/PB10: J15.26, RN2.5 (R4.2)
/PB11: J15.25
/PB12: J15.24, RN1.8 (R1.2)
/PB13: J15.23, RN1.7 (R2.2)
/PB14: J15.22, RN1.6 (R3.2)
/PB15: J15.21, RN1.5 (R4.2)
/PC0: J15.70
/PC1: J15.71
/PC6: J15.13, R6.1
/PC7: J15.12, R7.1
/PC8: J15.11
/PC9: J15.10
/PC10: J15.51
/PC11: J15.54
/PC13: J15.64, JP1.2 (C)
/PC14: J15.65, JP2.2 (C)
/PC15: J15.66, JP3.2 (C)
/PD5: J15.52
/PD6: J15.53
/PD13: J15.20
/PD14: J15.15
/PE0: J15.17
/PE1: J15.57
/PE2: J15.60
/PE4: J15.61
/PE5: J15.62
/PE6: J15.63
/PE10: J15.32
/PE12: J15.30
/PE13: J15.29, RN2.8 (R1.2)
/PE14: J15.28, RN2.7 (R2.2)
/PE15: J15.27, RN2.6 (R3.2)
/PF2: J15.38
/PF9: J15.67
/RS485_A: J5.2, J9.2, J15.43
/RS485_B: J5.1, J9.1, J15.44
/SWCLK: J14.2, J15.4, J17.7
/SWDIO: J14.1, J15.3, J17.6
/UART1A_RX: J3.2, J15.19
/UART1A_TX: J3.3, J15.59
/UART3B_RX: J21.4, RN2.3 (R3.1), U3.4
/UART3B_TX: J21.3, RN2.4 (R4.1), U3.6
/UART5_RX: J4.2, J15.58
/UART5_TX: J4.3, J15.18
GND: C1.2, C2.2, C3.2, C4.2, C5.2, C6.2, C7.2, C8.2, C9.2, C10.2, C11.2, C12.2, C13.2, D3.2 (A2), J1.1, J2.1, J3.1, J3.MP (MountPin), J4.1, J4.MP (MountPin), J5.MP (MountPin), J6.MP (MountPin), J7.MP (MountPin), J8.MP (MountPin), J9.MP (MountPin), J10.MP (MountPin), J11.MP (MountPin), J12.MP (MountPin), J13.MP (MountPin), J14.3, J14.MP (MountPin), J15.1, J15.34, J15.40, J15.41, J15.73, J15.78, J15.80, J16.1, J16.MP (MountPin), J17.2, J17.MP (MountPin), J18.1, J18.MP (MountPin), J19.1, J19.MP (MountPin), J20.1, J20.MP (MountPin), J21.2, J21.MP (MountPin), J23.1, J23.MP (MountPin), J25.2, J25.MP (MountPin), Q1.2 (S), Q2.2 (S), Q3.2 (S), Q4.2 (S), Q5.2 (S), R1.2, R12.2, R13.2, SW5.2, SW6.2, U1.2, U2.2, U3.2
unnamed: D2.3 (BK), R20.1
unnamed: D2.2 (GK), R18.1
unnamed: D2.1 (RK), R16.1
unnamed: J16.3, RN1.4 (R4.1), U2.3
unnamed: J18.3, RN1.3 (R3.1), U2.1
unnamed: J19.3, RN1.2 (R2.1), U2.6
unnamed: J20.3, RN1.1 (R1.1), U2.4
unnamed: J23.3, RN2.2 (R2.1), U3.1
unnamed: JP1.1 (A), JP2.1 (A), JP3.1 (A), R11.2
unnamed: JP1.3 (B), JP2.3 (B), JP3.3 (B), R12.1
unnamed: Q1.1 (G), R2.2
unnamed: Q2.1 (G), R14.2
unnamed: Q3.3 (D), R16.2
unnamed: Q4.3 (D), R18.2
unnamed: Q5.3 (D), R20.2
unnamed: R4.2, SW4.1
unnamed: R5.2, SW5.1
unnamed: R8.2, SW6.1
VBUS1: C4.1, D5.2 (A), J1.4
VBUS2: C3.1, D6.2 (A), J2.4

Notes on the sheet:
DO NOT USE
I2C4_SDA
Buttons
SWD
I2C4_SCL
LASER
Buzzer

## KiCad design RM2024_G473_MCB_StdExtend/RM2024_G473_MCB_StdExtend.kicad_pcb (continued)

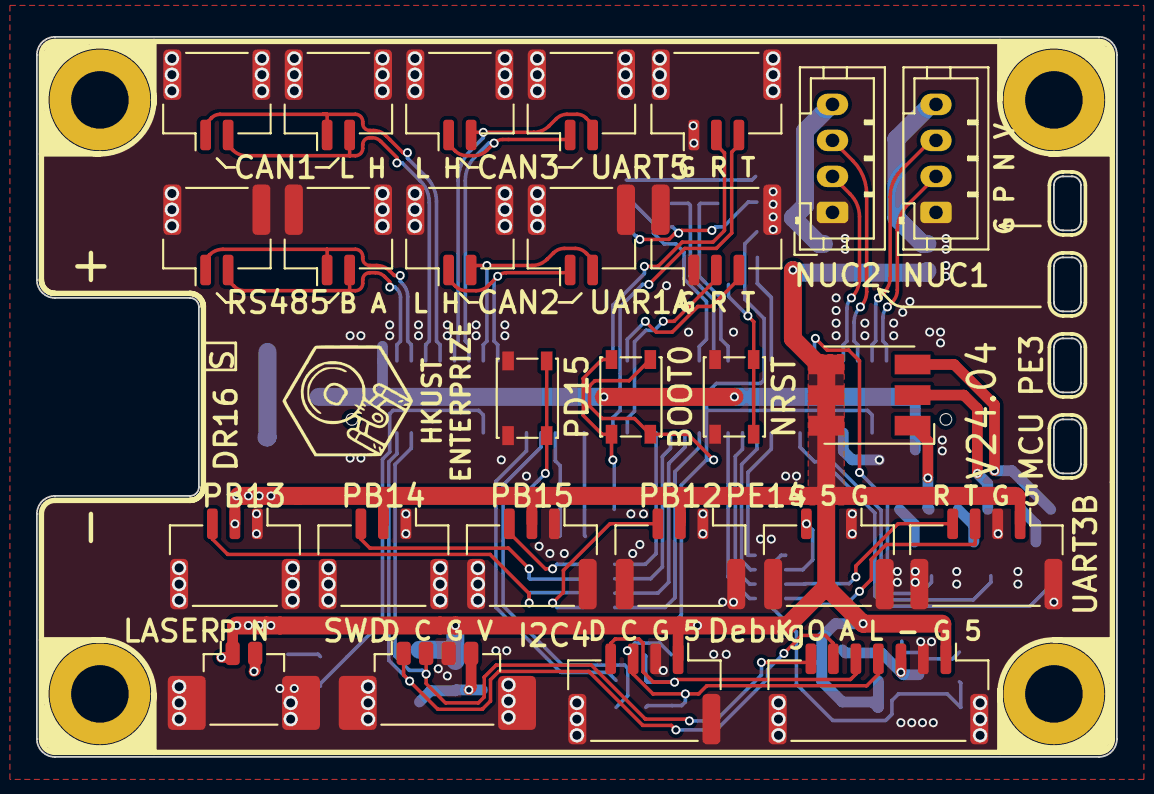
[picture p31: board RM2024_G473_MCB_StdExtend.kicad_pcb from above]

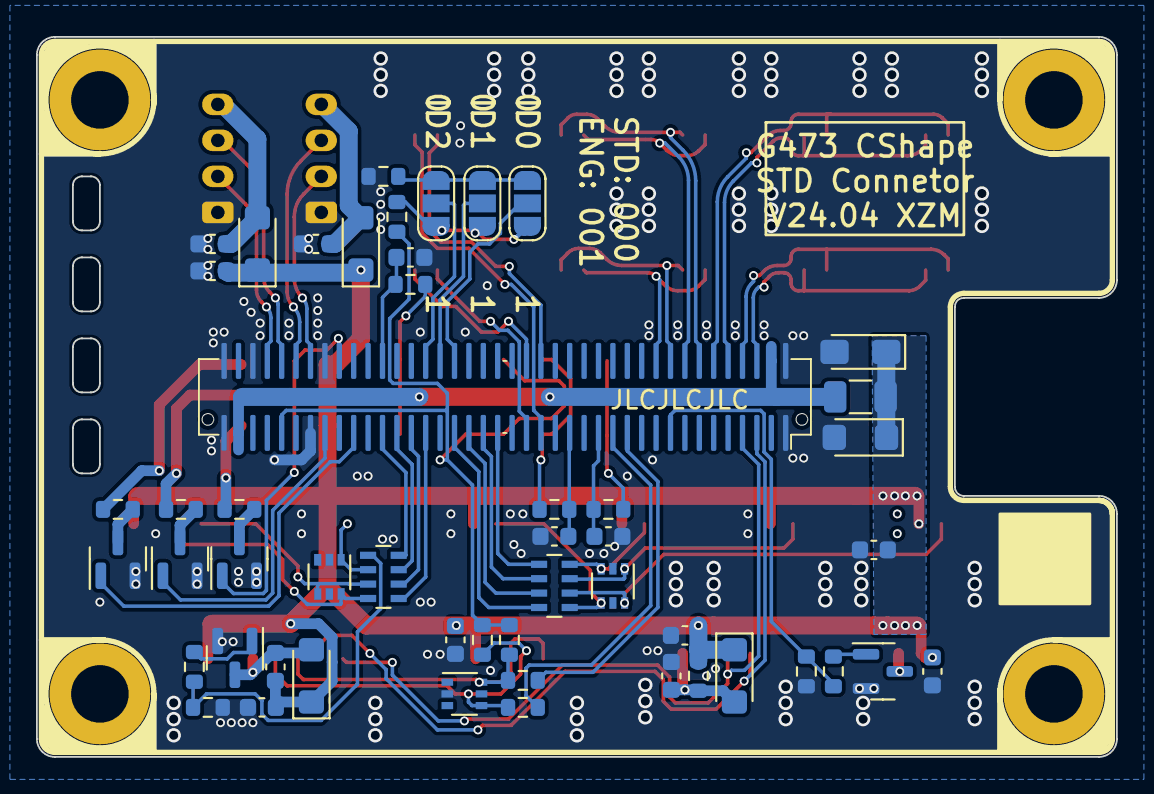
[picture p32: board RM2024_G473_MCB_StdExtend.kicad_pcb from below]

Board: 2 copper layers, 60.0 x 40.0 mm, 81 parts (50 on the bottom side), 71 nets.

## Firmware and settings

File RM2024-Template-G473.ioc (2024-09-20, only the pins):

Mcu.UserName=STM32G473VETx
PA0.Signal=USART2_CTS
PA1.Signal=USART2_RTS
PA10.GPIO_Label=UART1C_RX
PA10.Signal=USART1_RX
PA13.Signal=SYS_JTMS-SWDIO
PA14.Signal=SYS_JTCK-SWCLK
PA15.GPIO_Label=UART4_DE
PA15.Signal=UART4_DE
PA2.GPIO_Label=UART2A_TX
PA2.Signal=USART2_TX
PA3.GPIO_Label=UART2A_RX
PA3.Signal=USART2_RX
PA4.GPIO_Label=LIS3_CS
PA4.Signal=GPIO_Output
PA5.Signal=SPI1_SCK
PA6.Signal=SPI1_MISO
PA7.Signal=SPI1_MOSI
PB0.GPIO_Label=LIS3_DRY
PB0.Signal=GPXTI0
PB1.GPIO_Label=ICM_DRY
PB1.Signal=GPXTI1
PB10.GPIO_Label=UART3B_TX
PB10.Signal=GPIO_Output
PB12.Signal=SPI2_NSS
PB13.Signal=SPI2_SCK
PB14.Signal=SPI2_MISO
PB15.Signal=SPI2_MOSI
PB2.GPIO_Label=ICM_CS
PB2.Signal=GPIO_Output
PB3.Signal=FDCAN3_RX
PB4.Signal=FDCAN3_TX
PB5.Signal=FDCAN2_RX
PB6.Signal=FDCAN2_TX
PB8-BOOT0.GPIO_Label=BOOT0
PB8-BOOT0.Signal=GPIO_Input
PC0.GPIO_Label=ADC_POWER
PC0.Signal=GPIO_Output
PC1.GPIO_Label=ADC_5V
PC1.Signal=GPIO_Output
PC10.GPIO_Label=UART4_TX
PC10.Signal=UART4_TX
PC11.GPIO_Label=UART4_RX
PC11.Signal=UART4_RX
PC12.GPIO_Label=UART5_TX
PC12.Signal=UART5_TX
PC15-OSC32_OUT.GPIO_Label=LASER
PC15-OSC32_OUT.Signal=GPIO_Output
PC2.GPIO_Label=BUTTON
PC2.Signal=GPIO_Output
PC3.GPIO_Label=BUZZER
PC3.Signal=GPIO_Output
PD0.Signal=FDCAN1_RX
PD1.Signal=FDCAN1_TX
PD11.Signal=USART3_CTS
PD12.Signal=USART3_RTS
PD2.GPIO_Label=UART5_RX
PD2.Signal=UART5_RX
PD5.GPIO_Label=UART2B_TX
PD5.Signal=GPIO_Output
PD6.GPIO_Label=UART2B_RX
PD6.Signal=GPIO_Input
PD8.Signal=USART3_TX
PD9.Signal=USART3_RX
PE0.GPIO_Label=UART1B_TX
PE0.Signal=USART1_TX
PE15.GPIO_Label=UART3B_RX
PE15.Signal=GPIO_Input
PE3.GPIO_Label=LED_ACT
PE3.Signal=GPIO_Output
PF0-OSC_IN.Signal=RCC_OSC_IN
PF1-OSC_OUT.Signal=RCC_OSC_OUT
PF2.GPIO_Label=IMU_HEAT
PF2.Signal=S_TIM20_CH3
PG10-NRST.GPIO_Label=NRST
PG10-NRST.Signal=RCC_MCO
